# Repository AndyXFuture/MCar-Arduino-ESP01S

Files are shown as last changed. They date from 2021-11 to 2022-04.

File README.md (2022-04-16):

# MCar-Arudino-ESP01S
A Mecanum-wheel car based on ESP01S.

B站演示视频：https://www.bilibili.com/video/BV1oL4y1i7sb

制作教程视频：https://www.bilibili.com/video/BV1KR4y1b7LR



## 0. 关于本项目

因为看到up主@孟德尔の公主切的原理图中的TMI8549芯片只用一个引脚就可以控制一个轮，所以就突发奇想用正好只有四个GPIO的ESP01S来做一个麦轮小车，然后这个不到40元的项目就出来了

## 1.硬件打样说明

`Hardware`文件内有PCB板的AD源文件，可以直接发去打样，器件BOM有在表面的材料清单列出

因为ESP01S只有四个引脚所以8549这个芯片的使能脚我直接接的3.3V，然后通过PWM来控制正反转和停转，目前除了很吵之外没发现什么问题

焊接时可通过`ESP01S麦轮.html`来查看对应BOM表

## 2.固件编译说明

主要基于Arduino开发完成，根据下图的麦轮公式控制

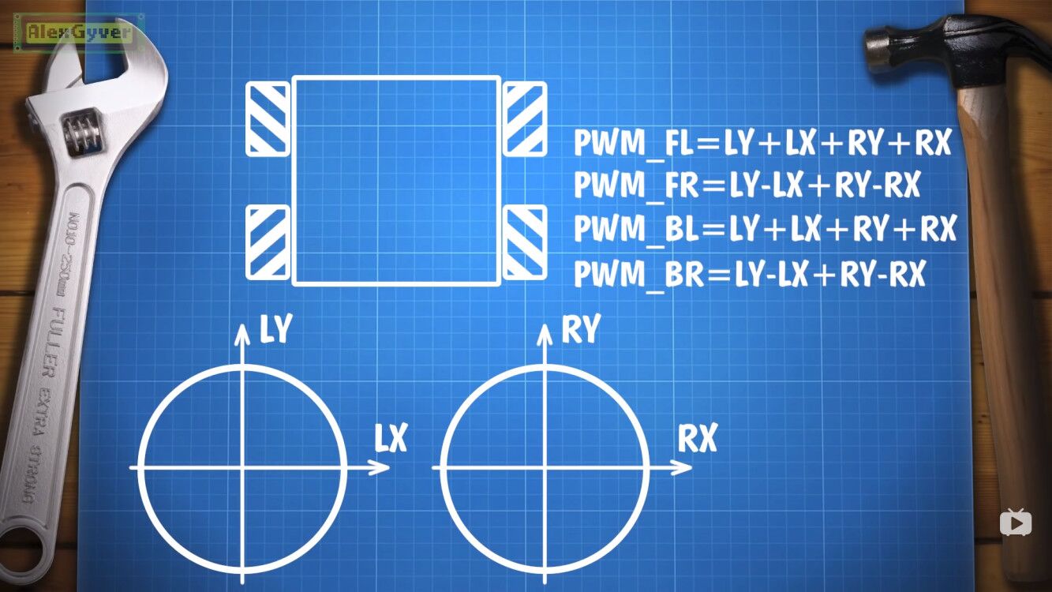
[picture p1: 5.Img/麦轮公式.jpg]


麦克纳姆轮，简称麦轮，是一种全方位轮，因为轮缘上`斜向`分布着许多小滚子，所以可以横向移动，通过四个轮子的协同控制可以完成很多动作，下图是从顶部观看的辊子方向，所以合力参考可以想象底部辊子的方向是这样“<>”

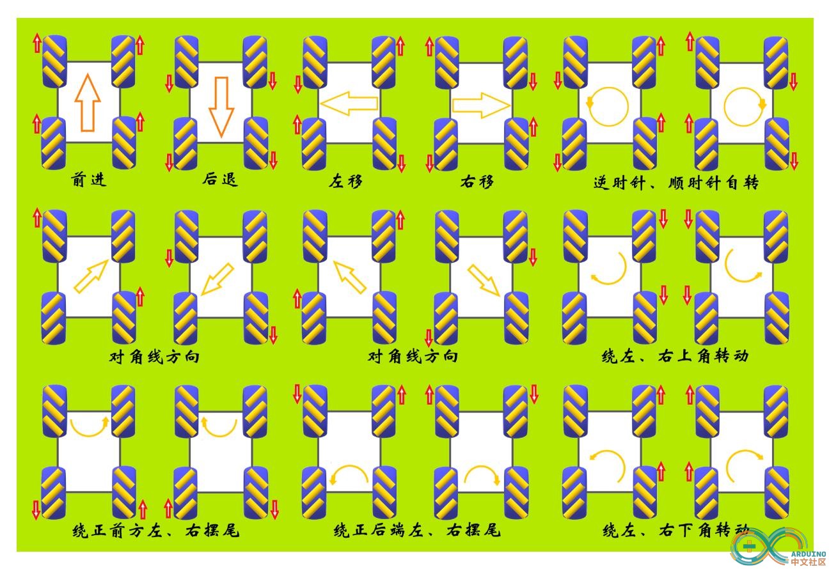
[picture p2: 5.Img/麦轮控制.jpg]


## 3.Android端程序说明

程序在`Software`文件夹里，目前只是能用就行的状态

程序内容大概就是两个摇杆加UDP广播，广播到9999端口，数据包的内容是四个0-32的数字，如：16161616就是两个摇杆回到原点的坐标，如果两个摇杆回到了原点就发一次16161616之后不再发包直到下一次摇杆变化

只需要将手机和模块连接到同一WIFI下，然后模块监听9999端口即可

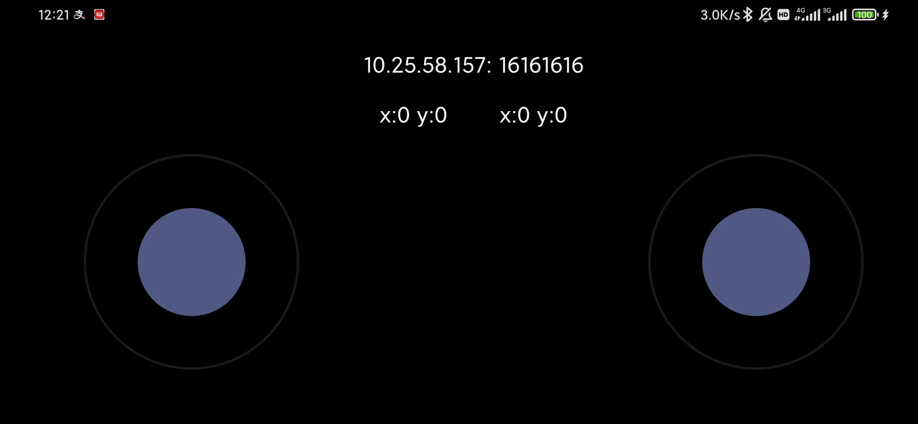
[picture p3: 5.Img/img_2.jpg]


## 4.麦轮制作说明

`Docs`文件夹里的压缩包里有B站up主@孟德尔の公主切开源的麦轮3D打印文件和装配说明，欢迎大家去给Ta的视频三连

https://www.bilibili.com/video/BV1wq4y1774g

>  `Docs`里面的`辊子100个.STL`是为了达到三维猴的壁厚要求自己用Solidworks画的，究极废手，谨慎使用，因为掰下来另一头是堵的，不止扩孔还得钻孔（泪目）搞定四个轮子花了一个晚上，需要的人多的话我再重新画一个版本吧

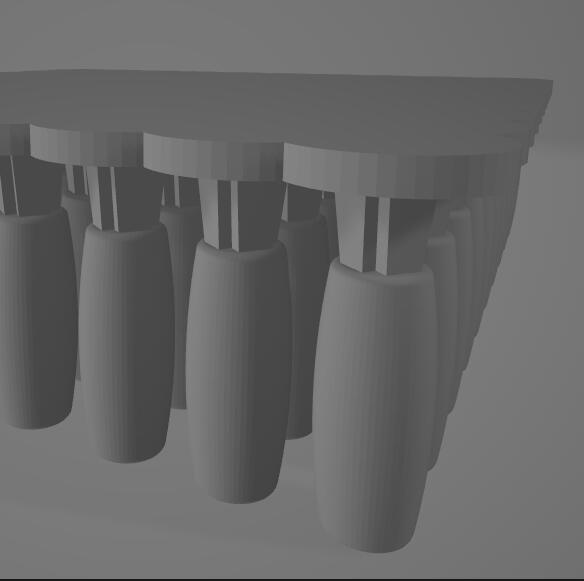
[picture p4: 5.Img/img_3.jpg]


## 5.关于这个项目的问题

首先是遥控的延迟（已修复）

> 感谢B站@27岁的188的指正，原因是运行到map()函数时参数没给好导致芯片重启了，没错就是重启了，过滤一下会导致错误的值便可以解决，开源代码中已修正。

然后是麦轮横移时的漂移，开始的时候是完全横移不动的，然后我做了两个措施就有了现在视频里的效果

1、我用电工胶布粘在电机的外壳和触点之间防止短路，这样就可以把电机座的螺丝拧死了，电机得以更加固定

2、将辊子拆下来，两头用磨砂纸打磨，用钻头又扩了一次孔，辊子转的更加顺畅

总的来说这个还是自制麦轮的弊端，只能是想办法增大摩擦力去搞定，无论是增大整车重量（压力）还是增大轮子表面的摩擦系数都会有一定程度改善

> ---

这个项目还有一些凭我个人能力解决不了或者没时间解决的问题在此列出来希望有专攻相应方面的大佬能提供思路

1、首先是停转时电机噪音较大的问题

这个是因为ESP01S`没有多余引脚去控制TMI8549的EN脚`，所以我只能给它拉高处理导致的，这个问题似乎还会使电流变大快速消耗电池电量所以也值得注意

正常来说停转的时候需要去给EN脚拉低，在不更换主控的前提下我钻牛角尖的方向主要有

硬件：本人没学过数电模电，所以只能想到用三极管去切换控制的电路实现引脚复用，但同时也因为没有引脚去控制三极管了所以在硬件方面暂时没有什么想法

MCU：因为ESP01S和ESP01的区别有个是启动的时候S不需要拉高EN脚，所以我想EN脚在什么情况下能够用起来，比如睡眠模式什么的，多一个引脚问题直接迎刃而解

总之还是钻牛角尖了，并且也想了解到对于这种引脚有限的情况有什么解决方法

2、电机转速无法跟摇杆的拉动距离去调整

因为麦轮的特性，每个轮子都要有不同的转速，程序里有个localMax值用来放大转速

因为让电机转起来首先就需要一定的扭力，没加放大的时候摇杆拉的近可能并不能让小车动起来，所以原作者可能基于这个考虑加了放大，按比例把转速放大，使其中一个轮的转速达到最大

问题有两点，一个是摇杆不会按拉动的距离去变速，另一个是对于转速比例低的轮子可能扭力并不能让它动起来，这样就导致移动的方向和想要的方向有偏差

解决方法就是设一个扭力驱动的最小值，让转速在这个最小值和最大值之间映射便可以解决，但我个人暂时没这两个需求，所以把解决思路放这里先了

3、麦轮摩擦力不够，去淘宝8.5一个买四个麦轮可以解决，但联轴器我仿照麦轮手册的联轴器画了一版给这个电机的，发现很容易断，不是打印件断而是让电机断，所以如果要上成品麦轮应该得换电机

在此放上成品麦轮的电机，我买的是48mm无接口的，我画的联轴器放Docs文件夹里了

https://item.taobao.com/item.htm?spm=a1z09.2.0.0.1ef12e8dYhUjfD&id=597783667844&_u=g389riah1755

## 其他的后续再补充，欢迎大家给视频点赞~

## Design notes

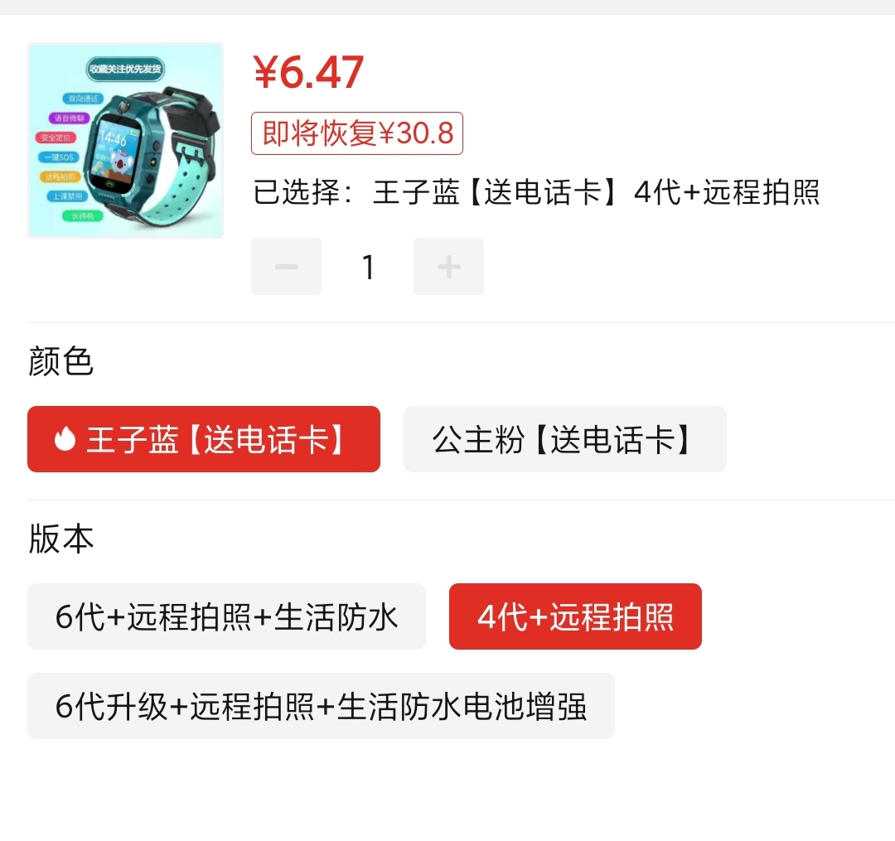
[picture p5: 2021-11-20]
5.Img/嫖电池.jpg

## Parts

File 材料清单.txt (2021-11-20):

ESP01S                 6元  拼多多随便找个就行

麦轮部分
3D打印                 20元以内
	3D打印文件在BV1wq4y1774g这个视频下有下载链接
	3D打印我之前是在捷配白嫖的（连邮费都不用），现在好像不发那个3D打印券了
	嫖不了就去闲鱼找个光固化代打，也可以去淘宝的新客免费，还有嘉立创的三维猴（单件2元起）
	以上几个地方加上邮费基本可以在20元以内可以搞定

PCB部分
嘉立创PCB打样		免费
AMS1117-3.3V		  0.25元
https://item.taobao.com/item.htm?spm=a1z10.3-c-s.w4002-21223910208.9.4be16a4bxZfW4U&id=522572478170
充电模块                2.9元
https://item.taobao.com/item.htm?spm=a1z0d.6639537.1997196601.22.4cf37484OIYDYe&id=585192851651
Type-C接口6pin	       0.25元
https://item.taobao.com/item.htm?spm=a1z0d.6639537.1997196601.4.5fca7484hGrDiB&id=573089663803
LV8549*2               2.2元*2
https://item.taobao.com/item.htm?spm=a1z09.2.0.0.24df2e8dOqxKvm&id=599116196858&_u=p389riah7775
3.7V锂电池（从小天才电话手表拆）   1.8元
（拼多多6.8元返现5元具体看资料里的图/5.Img/嫖电池.jpg）

M10电机                2-3元*4
跟着麦轮制作的装配说明文档以图搜货就行，我买的那家不包邮就不放链接了
https://s.taobao.com/search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

其他（价格按单个算几乎忽略不计）
硅胶管3*4mm
得力3号大头针
以下都可以在优信电子这家淘宝店找到
1mm钻头（用来扩孔）
电工胶布或其他胶布（用来防止触点碰到金属外壳短路）
螺丝（M2*5）
螺母（M2）
排针、排母
0.1uf(100nf) 贴片电容（0603）
10uf 贴片电容（0603）
10k 贴片电阻（0603）

工具
电烙铁、焊锡丝、串口烧录器

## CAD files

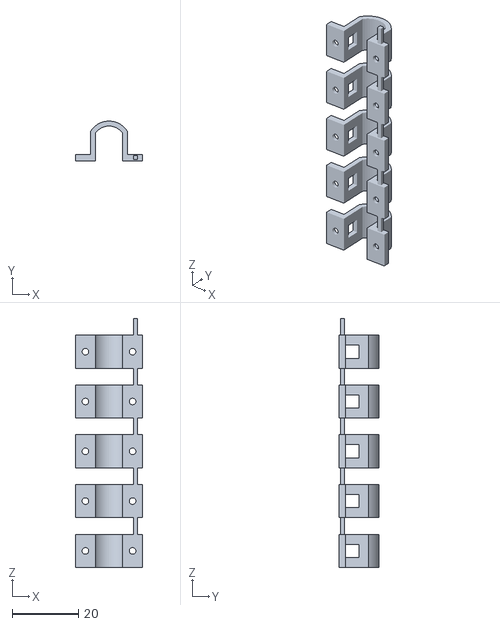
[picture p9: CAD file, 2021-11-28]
4.Docs/电机座5个一体.STL
20.2 x 12.0 x 75.0

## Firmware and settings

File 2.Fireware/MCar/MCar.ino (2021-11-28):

#include <ESP8266WiFi.h>
#include <WiFiUdp.h>
//#include "Ticker.h"

#define PWM_M1  0
#define PWM_M2  1
#define PWM_M3  2
#define PWM_M4  3

//Ticker ticker;
int AX,AY,BX,BY;
int M1_Speed,M2_Speed,M3_Speed,M4_Speed;
int local_max;

const char* ssid = "your ssid";
const char* password = "your password";

WiFiUDP Udp;
unsigned int localUdpPort = 9999;
char incomingPacket[255];

void flash(){
     M1_Speed=(BY-BX-AX+AY)/4;
     M2_Speed=(BY+BX+AX+AY)/4;
     M3_Speed=(BY-BX+AX+AY)/4;
     M4_Speed=(BY+BX-AX+AY)/4;


     local_max=abs(M1_Speed);
     local_max=max(abs(M2_Speed),local_max);
     local_max=max(abs(M3_Speed),local_max);
     local_max=max(abs(M4_Speed),local_max);
     if(local_max == 0){
        local_max = 16;
     }
     //映射
     M1_Speed=map(M1_Speed,-local_max,local_max,0,1023);
     M2_Speed=map(M2_Speed,-local_max,local_max,1023,0);
     M3_Speed=map(M3_Speed,-local_max,local_max,1023,0);
     M4_Speed=map(M4_Speed,-local_max,local_max,0,1023);

     analogWrite(PWM_M1,M1_Speed);
     analogWrite(PWM_M2,M2_Speed);
     analogWrite(PWM_M3,M3_Speed);
     analogWrite(PWM_M4,M4_Speed);
}


void setup()
{
  pinMode(PWM_M1, OUTPUT);
  pinMode(PWM_M2, OUTPUT);
  pinMode(PWM_M3, OUTPUT);
  pinMode(PWM_M4, OUTPUT);
  analogWrite(PWM_M1,512);
  analogWrite(PWM_M2,512);
  analogWrite(PWM_M3,512);
  analogWrite(PWM_M4,512);
  
  WiFi.begin(ssid, password);
  while (WiFi.status() != WL_CONNECTED)
  {
    delay(500);
  }

  Udp.begin(localUdpPort);
  
  //ticker.attach_ms(50,flash);
}
void loop()
{
  if (Udp.parsePacket())//解析包不为空
  {
    memset(incomingPacket, 0, sizeof(incomingPacket));
    Udp.read(incomingPacket,255);

    //解析
    int Data = atoi(incomingPacket);
    AX = Data/1000000-16;
    AY = (Data/10000)%100-16;
    BX = (Data/100)%100-16;
    BY = Data%100-16;

    flash();
  }
}

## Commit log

2021-11-20 Update 材料清单
2021-11-26 Update 可交互式HTML-BOM表
2021-11-28 解决滞后问题
    （修复了map()导致重启的问题）
2021-12-06 清理多余文件
